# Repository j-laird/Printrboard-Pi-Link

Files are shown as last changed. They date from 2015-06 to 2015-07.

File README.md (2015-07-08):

# Printrboard-Pi-Link
Printed Circuit Board Assembly linking a Printrbot Printrboard and Raspberry Pi

Printrboard Pi Link

## Overview

The Printrboard-Pi-Link is intended to connect a Printrbot Printrboard with a newer-model Raspberry Pi (B+, Raspberry Pi 2 B, etc).  It has the following unique features:
* Accepts 12v input on either 4-pin(ATX 12V) or 6-pin(PCI-E) Molex Minifit-Jr connectors
* Supplies switched (see below) 12V power to Printrboard via screw-type Phoenix connector
* Produces high-current (3A max) 5V power for Raspberry Pi (no wall-wart needed)
* Uses UART connection on Raspberry Pi GPIO (replaces micro-USB connection to Printrboard)
* Exposes 3 GPIO intended for:
  * Printrbot "ready to print" LED
  * Printrbot "push to print" button
  * Wi-Fi mode switch between AP and infrastructure mode
* Allows the Raspberry Pi to shutoff 12V power to Printrboard (in case bad things happen)
* Exposes an external safety 12v shutoff for user-supplied circuits (smoke detector, etc.)
* Adds automotive-style ATO fuse in 12V path

### BUILD INFORMATION

All parts but L1 (inductor) can be sourced from Digikey. A pre populated [shopping cart](http://www.digikey.com/short/71w84q) with enough parts to build this (minus ribbon cable and 16awg wire) is available.   NOTE THIS CART IS FOR REV B.  Rev A used a different fuse holder.

[Bill of Materials](https://docs.google.com/spreadsheets/d/1JWQViEhnYA_FKTI_PxGergLy6LZkPQN6mZyLyM8gfQU/edit?usp=sharing)

### CONFIGURATION

When creating the Printrboard-Pi-Link, I recognized that some printrbot models "hide" the Printrboard underneath the printer, while others leave the board exposed.  When this board is installed on the Raspberry Pi, only two cables need be connected from this board to the Printrboard: a ribbon cable to EXP1, and a 4/6-wire power cable to the power connection.  

It is expected that a short ribbon cable can be supplied for users who want the Raspberry Pi located back-to-back with the Printrboard, and a longer ribbon cable can be supplied for those "hidden" Printrboards.  Similarly, the supplied 4 or 6-pin power extension has only a connector on one end -- and can be cut to length by the customer (thus the screw terminals).

### FIRMWARE

In order to enable the hardware UART on the Printrboard (rather than the USB CDC serial port), use of this board requires a special build of firmware.  Standard firmware versions will not communicate directly, although it would be possible to communicate using the traditional micro USB cable to one of the Raspberry Pi's USB ports.

* [Rev D Firmware](https://github.com/j-laird/Marlin/releases/tag/PiBachelor--V3)
* [Rev F4/F5 Firmware](https://github.com/j-laird/Marlin/releases/tag/PiLassen-V3)

### RASPBERRY PI / OCTOPRINT SETUP

The hardware UART on the RPI must be enabled.  Run raspi-config and select Advanced Options.  Under Serial, disable login over serial port.

Modify /boot/config.txt to add init_uart_clock=4000000

Install WiringPi using the following [instructions](https://projects.drogon.net/raspberry-pi/wiringpi/download-and-install/).

Modify ~/.octoprint/config.yaml to add the following lines under system: actions:

    - action: shutdown printbot
      command: gpio -g write 2 1
      name: Kill Printrboard 12V supply
    - action: poweron printrbot
      command: gpio -g write 2 0
      name: Enable Printrboard 12V supply

Modify /etc/init.d/octoprint to add the following lines in the do_start() function, right above RETVAL="$?"

    gpio -g export 2 out
    gpio -g mode 2 out
    gpio -g write 2 0

## DISCLAIMERS

Although using a Raspberry Pi with [Octoprint](http://octoprint.org/) is a fabulous way to run a print job semi-unattended, and this board enables additional features in that regard, it is **categorically not endorsed/recommended** as a safe practice.  The additional safety and remote shutdown features should not encourage you to leave the printer at home/work printing.  For those of you who void warranties, tear up manuals, and eat your steak rare -- hopefully this provides additional safety margin.

But seriously - don't print unattended.

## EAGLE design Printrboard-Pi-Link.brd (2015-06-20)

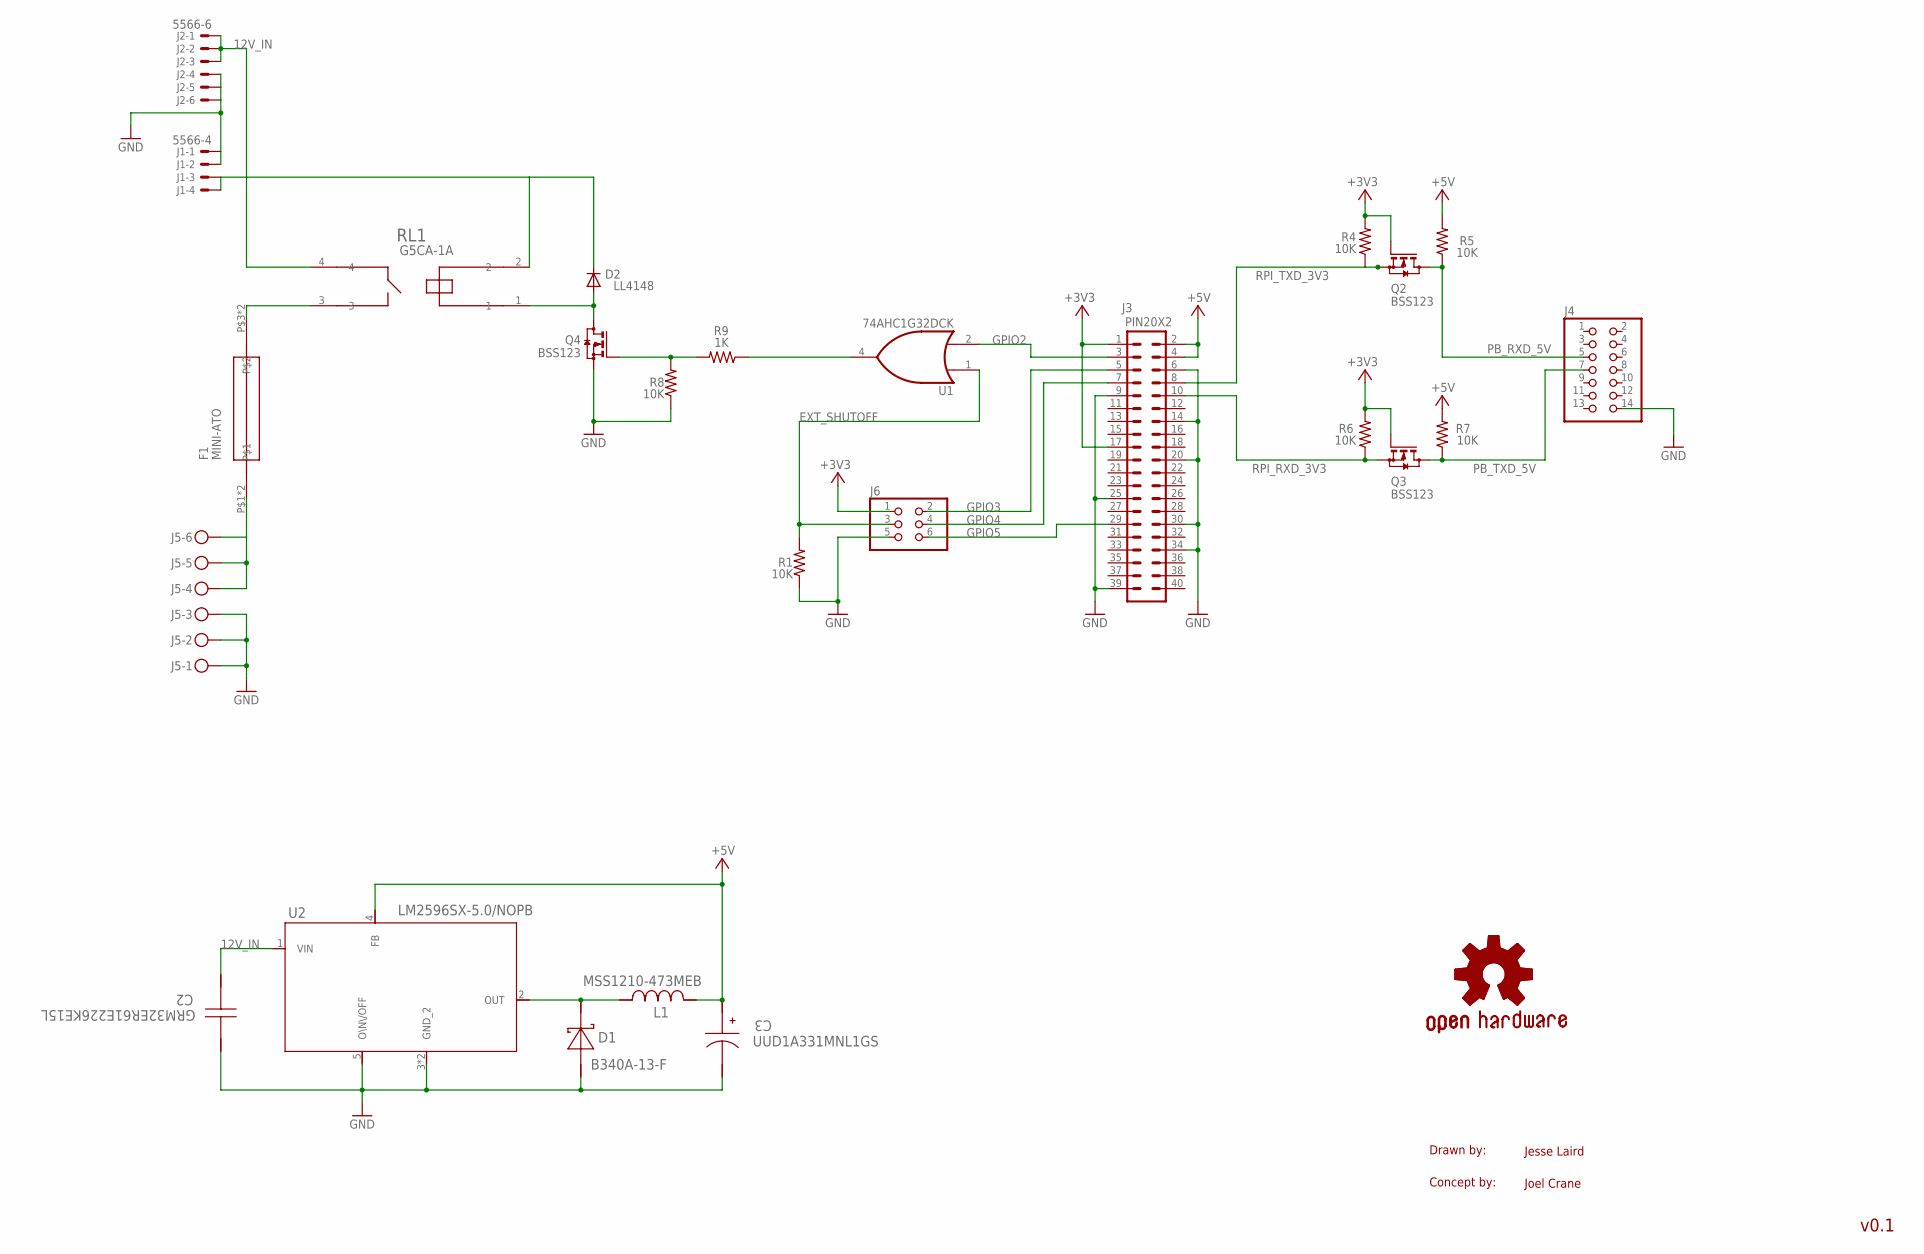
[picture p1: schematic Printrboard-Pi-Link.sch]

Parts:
C2: GRM32ER61E226KE15L; 1210
C3: UUD1A331MNL1GS; SM_RADIAL_8MM
D1: B340A-13-F; SMA
D2: LL4148; SOD80C
F1: MINI-ATO; BK-6011
GOLD_ORB_SM1: OSHWLOGO_GOLD_ORB_SM; OSHW2
J1: 5566-4
J2: 5566-6
J3: PIN20X2; PIN_20X2
J4: PINHD-2X7; 2X07
J5: MKDSN1,5/6-5,08
J6: PINHD-2X3; 2X03
L1: MSS1210-473MEB; MSS1210
Q2, Q3, Q4: BSS123; SOT23
R1, R4, R5, R6, R7, R8: 10K; R0603
R9: 1K; R0603
RL1: G5CA-1A; G5CA
U1: 74AHC1G32DCK; SC70-5
U2: LM2596SX-5.0/NOPB; TS5B

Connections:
12V_IN: C2.1, D2.C, J1.3, J1.4, J2.1, J2.2, J2.3, RL1.2, RL1.4, U2.1 (VIN)
+3V3: J3.1, J3.17, J6.1, Q2.1 (G), Q3.1 (G), R4.2, R6.2
+5V: C3.1 (+), J3.2, J3.4, L1.2, R5.2, R7.2, U2.4 (FB)
EXT_SHUTOFF: J6.3, R1.2, U1.1 (I0)
GND: C2.2, C3.2 (-), D1.2 (A), J1.1, J1.2, J2.4, J2.5, J2.6, J3.6, J3.9, J3.14, J3.20, J3.25, J3.30, J3.34, J3.39, J4.14, J5.1, J5.2, J5.3, J6.5, Q4.2 (S), R1.1, R8.1, U1.3 (GND), U2.3 (GND_2), U2.5 (O\N\/OFF), U2.6 (GND_2)
GPIO2: J3.3, U1.2 (I1)
GPIO3: J3.5, J6.2
GPIO4: J3.7, J6.4
GPIO5: J3.29, J6.6
unnamed: F1.P$3, F1.P$4, RL1.3
unnamed: R9.1, U1.4 (O)
unnamed: D1.1 (K), L1.1, U2.2 (OUT)
unnamed: D2.A, Q4.3 (D), RL1.1
unnamed: Q4.1 (G), R8.2, R9.2
unnamed: F1.P$1, F1.P$2, J5.4, J5.5, J5.6
PB_RXD_5V: J4.5, Q2.3 (D), R5.1
PB_TXD_5V: J4.7, Q3.3 (D), R7.1
RPI_RXD_3V3: J3.10, Q3.2 (S), R6.1
RPI_TXD_3V3: J3.8, Q2.2 (S), R4.1
VCC: U1.5 (VCC)

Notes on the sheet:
Drawn by:
Concept by:
Jesse Laird
v0.1
Joel Crane

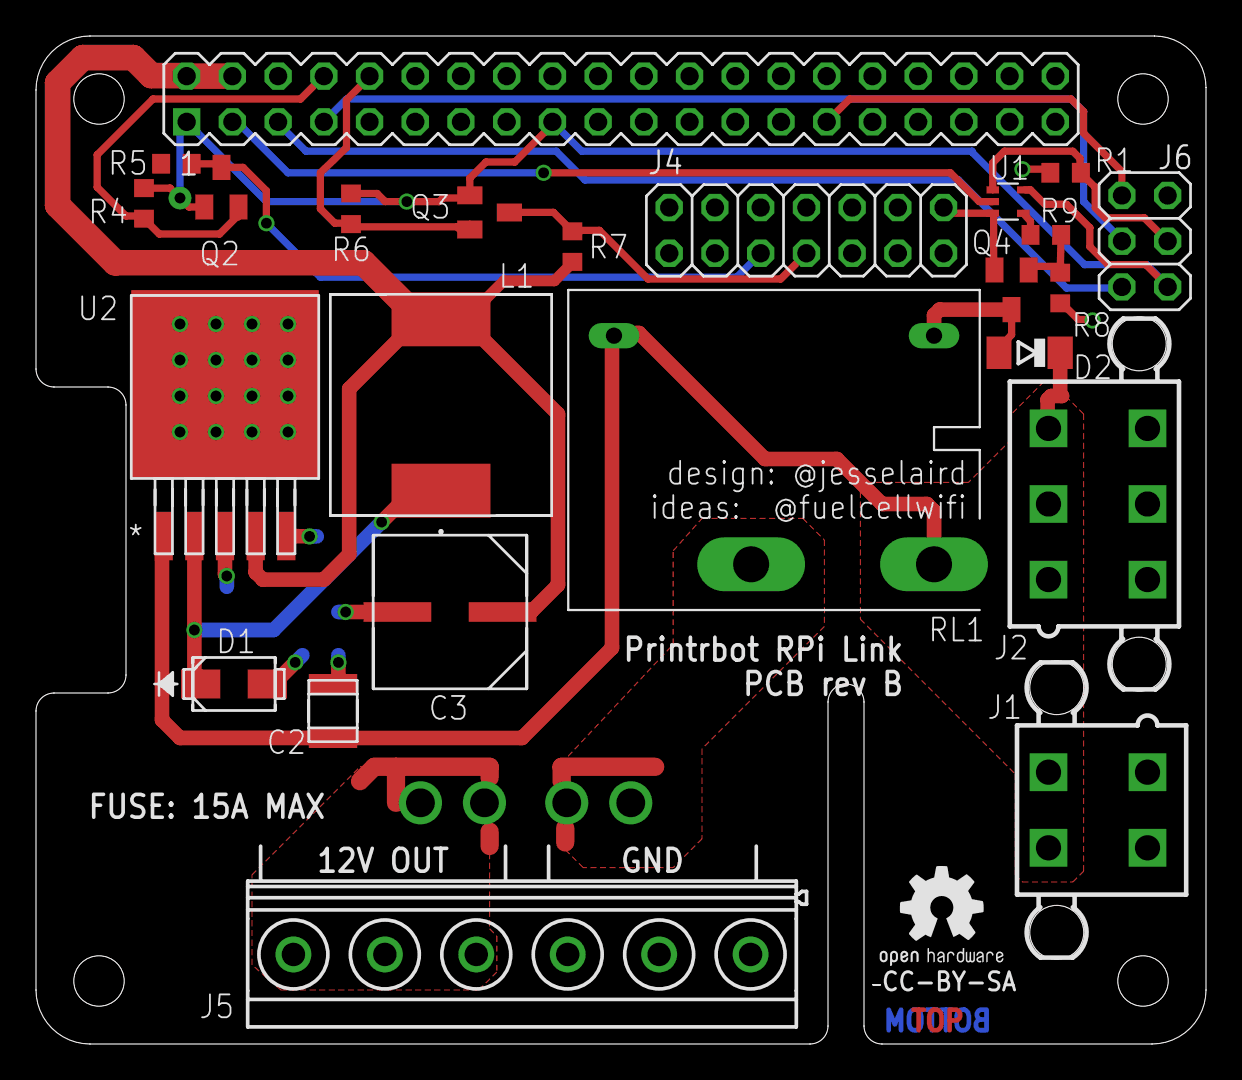
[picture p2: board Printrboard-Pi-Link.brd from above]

Board: 2 copper layers, 65.0 x 56.0 mm, 26 parts (0 on the bottom side), 19 nets.

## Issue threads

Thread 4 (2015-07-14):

PCB

eboston, 2015-07-14:
Is the latest rev of the board available at OSHPark in the shared projects?

j-laird, 2015-07-16:
Not yet.  I've got just 9 prototypes out in the world and would like to get feedback on these and possibly revise the board first.  Of course, the rev B Getber files are posted in the repository, so there is nothing stopping you from downloading them and ordering through Oshpark or the vendor of your choice.

eboston, 2015-07-16:
I was looking at the Eagle files and noticed several of the pins on the
GPIO connector that are suppose to go to ground are not connected.  Was
it done this way on purpose or is the Eagle board file just out of date?

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

arcmatt, 2018-01-08:
What ever happened to this project/product?

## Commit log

2015-05-22 First Fabrication - Rev A
    First fabrication @ OSHPARK
    [Printrboard-Pi-Link.brd, Printrboard-Pi-Link.sch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]
2015-06-18 Added Digikey BOM
    Added Digikey cart for components
2015-06-20 Rev_B
    Fixes missing 3v3 connection on NOR gate; reduces fuse size from ATO to
    mini-ATO/automotive fuse.
    [Printrboard-Pi-Link.brd, Printrboard-Pi-Link.sch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]
2015-06-26 Added firmware links and wiringPi setup
2015-06-27 Added Google Docs BOM
2015-07-07 Update links and headings, add PCBA photo, make octoprint settings section code

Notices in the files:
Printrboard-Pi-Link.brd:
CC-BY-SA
